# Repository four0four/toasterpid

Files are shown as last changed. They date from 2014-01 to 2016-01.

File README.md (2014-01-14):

# toasterpid

Firmware for my reflow oven PID controller (WIP!)

## Complete:
+ Simple serial driver
+ Thermocouple driver
+ LCD driver (4-bit, 8-bit)

## Work in progress:
+ PID algorithm/tuning
  + PID values don't differ much from 0 or 255, and given the oven's thermal momentum, they shouldn't...
+ Testing: Insulation in the oven

## Entirely untouched:
+ User interface

## Potential features:
+ USB instead of serial (final version will use an atmega16u4 or similar)
+ Serial (or USB) control

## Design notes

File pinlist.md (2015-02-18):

## AVR atmega168 pin listing

### Port B
+ Bit 0 - NC
+ Bit 1 - NC 
+ Bit 2 - uSD CS
+ Bit 3 - SPI MOSI
+ Bit 4 - SPI MISO
+ Bit 5 - SPI CLK
+ Bit 6 - AVR clk input (from enc28j60)
+ Bit 7 - SSR output (can we do this with clkin on b6?)

### Port C
+ Bit 0 - NC
+ Bit 1 - LCD EN
+ Bit 2 - LCD RS
+ Bit 3 - LCD R/W
+ Bit 4 - PHY reset
+ Bit 5 - PHY interrupt
+ Bit 6 - AVR reset
+ Bit 7 - Not pinned out

### Port D
+ Bit 0 - LCD bus bit 4 (0 in 4bit)
+ Bit 1 - LCD bus bit 5 (1 in 4bit)
+ Bit 2 - LCD bus bit 6 (2 in 4bit)
+ Bit 3 - LCD bus bit 7 (3 in 4bit)
+ Bit 4 - PHY CS
+ Bit 5 - Daughter CS (Thermo amp CS)
+ Bit 6 - Daughter LED 1
+ Bit 7 - Daughter LED 2

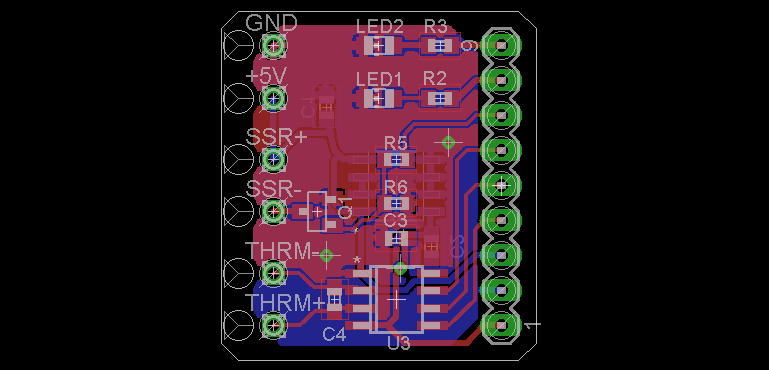
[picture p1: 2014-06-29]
hardware/images/daughter-brd.png

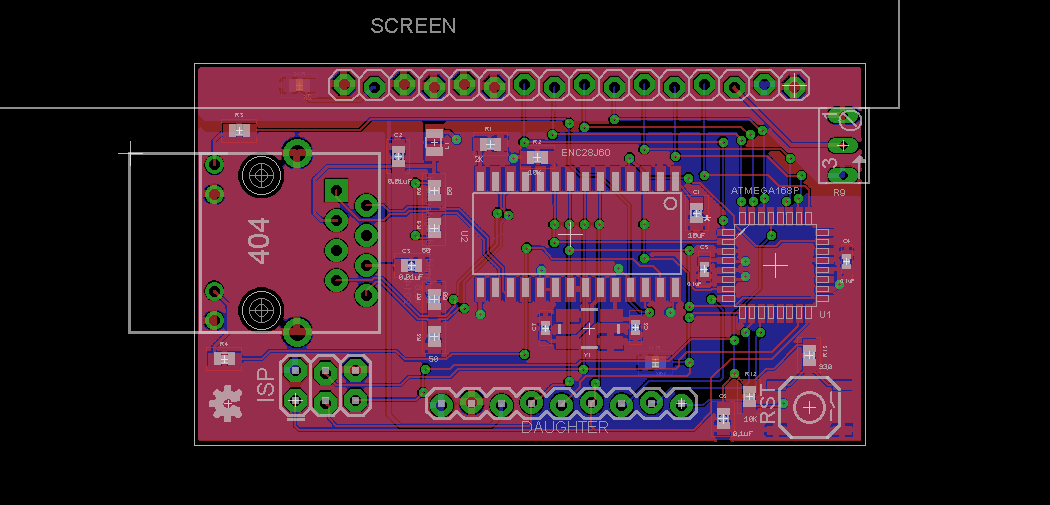
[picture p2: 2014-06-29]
hardware/images/main-brd.png

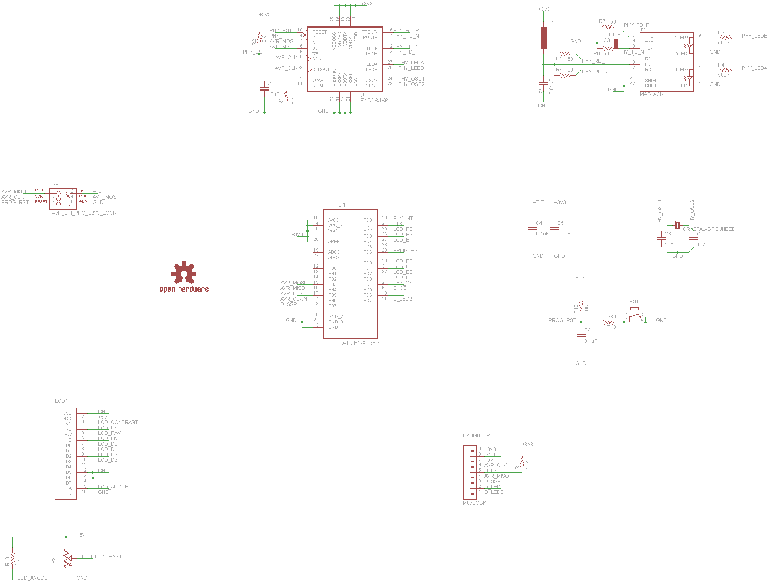
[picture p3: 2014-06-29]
hardware/images/main-sch.png

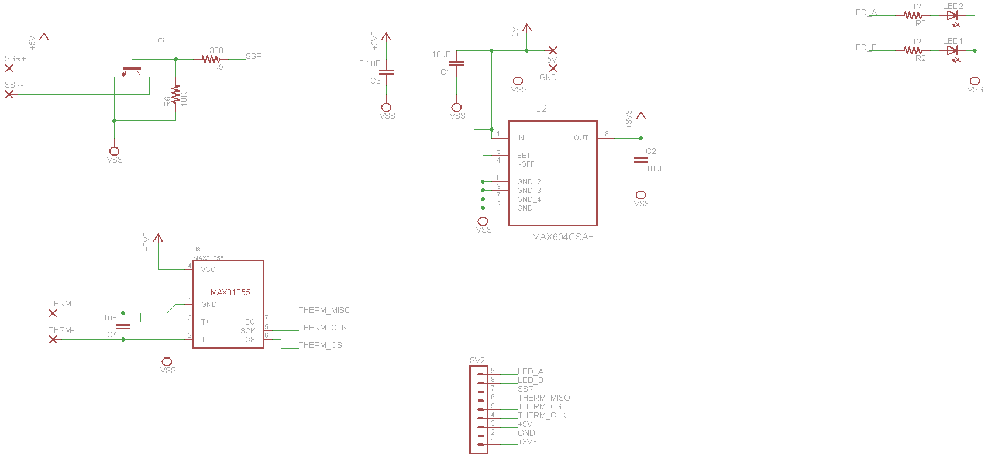
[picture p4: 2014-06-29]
hardware/images/daughter-sch.png

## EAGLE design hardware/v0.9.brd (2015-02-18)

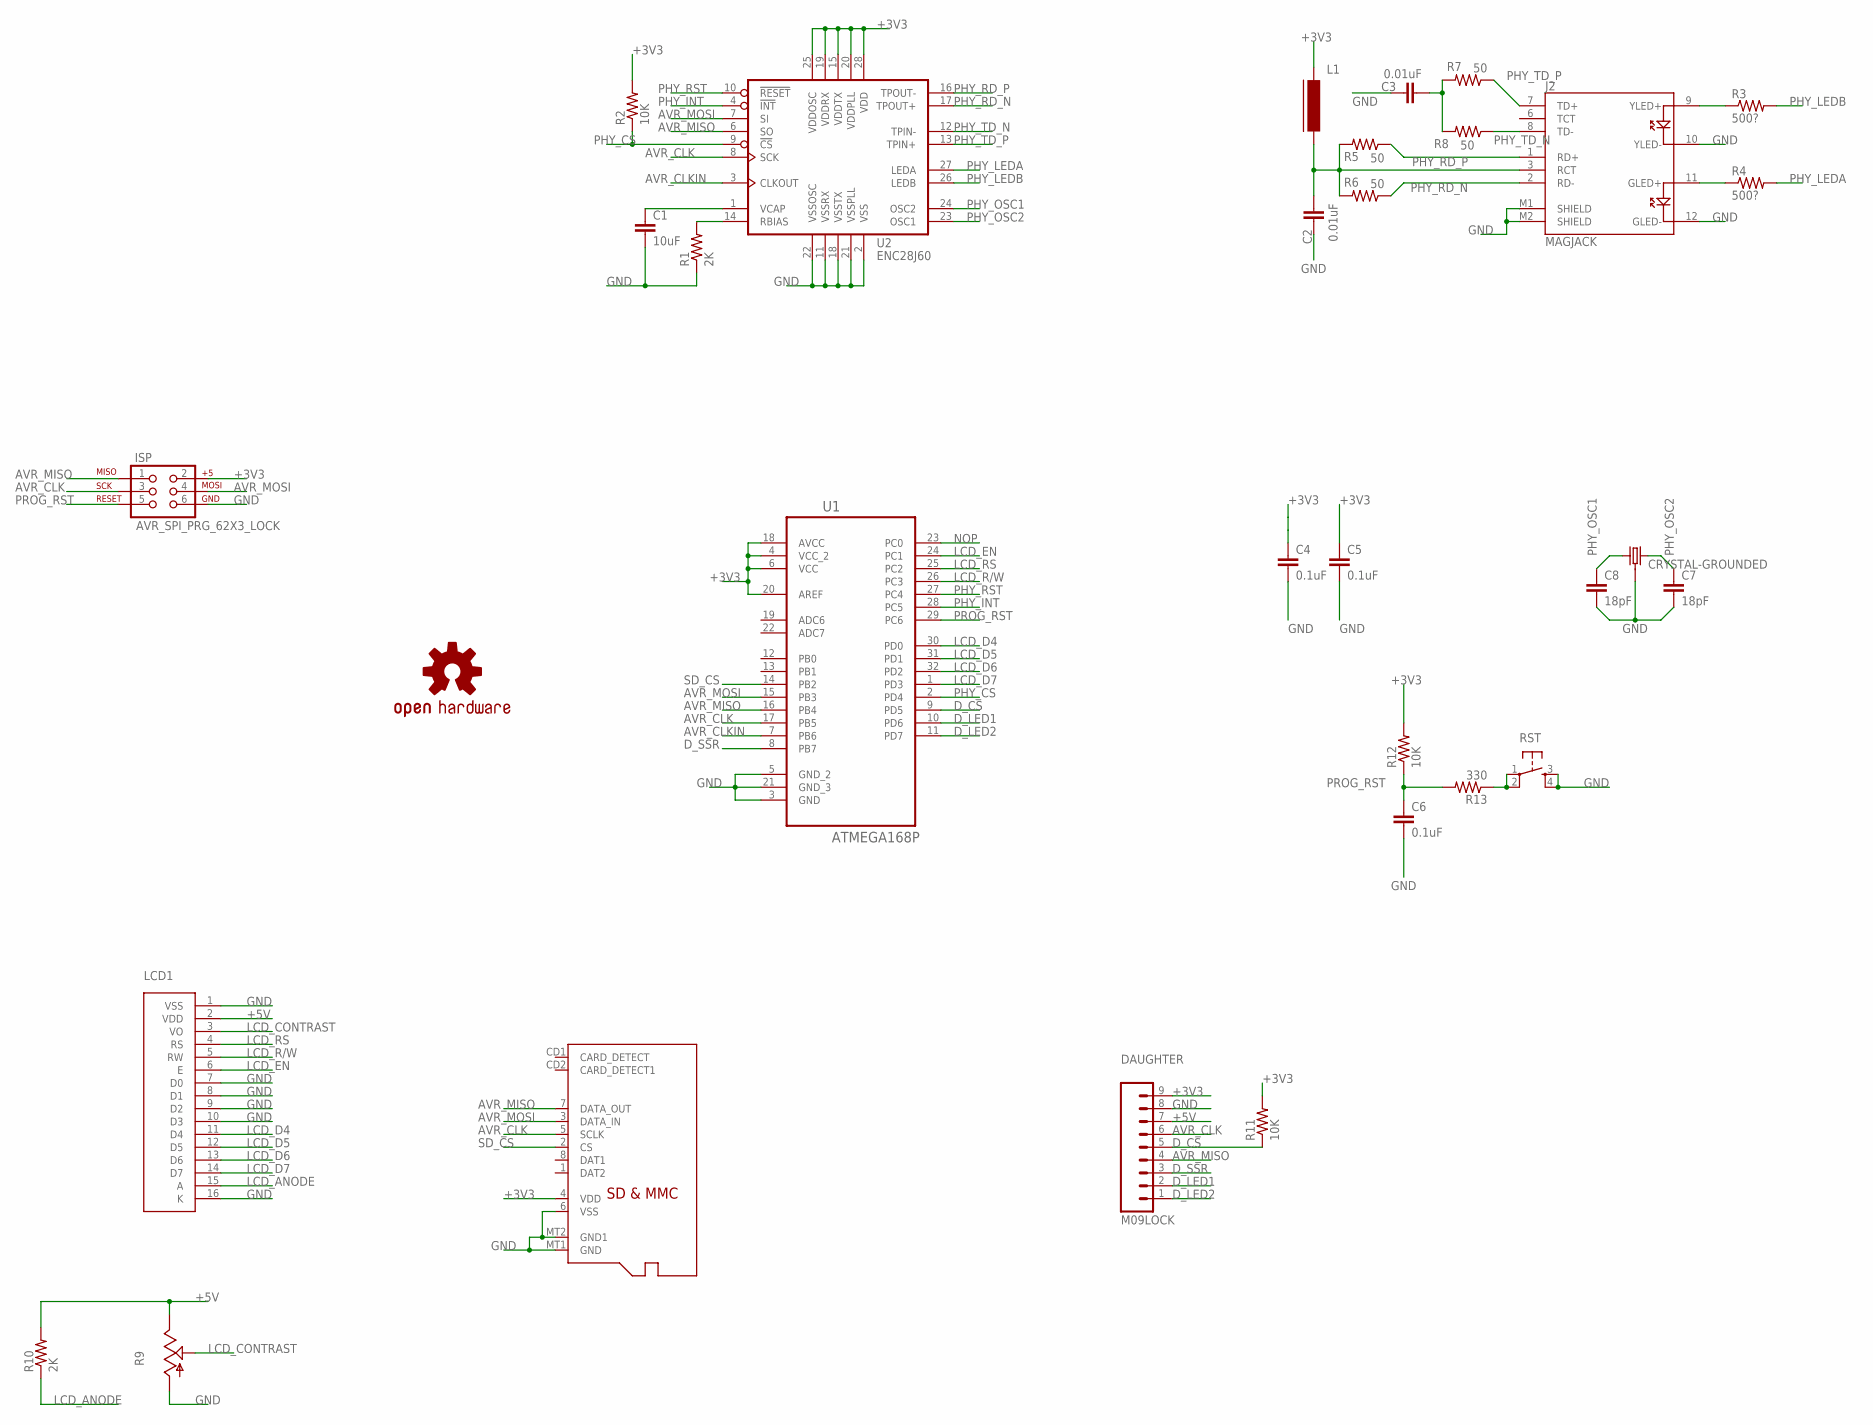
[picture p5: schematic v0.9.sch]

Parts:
C1: 10uF; 0603-CAP
C2, C3: 0.01uF; 0603-CAP
C4, C5: 0.1uF; 0402-CAP
C6: 0.1uF; 0603-CAP
C7, C8: 18pF; 0402-CAP
DAUGHTER: M09LOCK; 1X09_LOCK
ISP: AVR_SPI_PRG_62X3_LOCK; 2X3_LOCK
J2: MAGJACK
L1: FERRITE-0603; FB603
LCD1: HD44780; .1"16PIN
LOGO1: OSHW-LOGOS; OSHW-LOGO-S
R1, R10: 2K; 0603-RES
R2, R11, R12: 10K; 0603-RES
R3, R4: 500?; 0603-RES
R5, R6, R7, R8: 50; 0603-RES
R9: TRIM_US-B64Y; B64Y
R13: 330; 0603-RES
RST: TAC_SWITCHSMD; TACTILE-SWITCH-SMD
SD: MICROSD
U1: ATMEGA168P; QFP80P900X900X120-32N
U2: ENC28J60; SOIC-28W
Y1: CRYSTAL-GROUNDED; CRYSTAL-SMD-5X3

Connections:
+3V3: C4.1, C5.1, DAUGHTER.9, ISP.2, L1.1, R2.2, R11.2, R12.2, SD.4 (VDD), U1.4 (VCC_2), U1.6 (VCC), U1.18 (AVCC), U1.20 (AREF), U2.15 (VDDTX), U2.19 (VDDRX), U2.20 (VDDPLL), U2.25 (VDDOSC), U2.28 (VDD)
+5V: DAUGHTER.7, LCD1.2 (VDD), R9.E, R10.2
AVR_CLK: DAUGHTER.6, ISP.3, SD.5 (SCLK), U1.17 (PB5), U2.8 (SCK)
AVR_CLKIN: U1.7 (PB6), U2.3 (CLKOUT)
AVR_MISO: DAUGHTER.4, ISP.1, SD.7 (DATA_OUT), U1.16 (PB4), U2.6 (SO)
AVR_MOSI: ISP.4, SD.3 (DATA_IN), U1.15 (PB3), U2.7 (SI)
D_CS: DAUGHTER.5, R11.1, U1.9 (PD5)
D_LED1: DAUGHTER.2, U1.10 (PD6)
D_LED2: DAUGHTER.1, U1.11 (PD7)
D_SSR: DAUGHTER.3, U1.8 (PB7)
GND: C1.2, C2.1, C3.1, C4.2, C5.2, C6.2, C7.2, C8.2, DAUGHTER.8, ISP.6, J2.10 (YLED-), J2.12 (GLED-), J2.M1 (SHIELD), J2.M2 (SHIELD), LCD1.1 (VSS), LCD1.7 (D0), LCD1.8 (D1), LCD1.9 (D2), LCD1.10 (D3), LCD1.16 (K), R1.1, R9.A, RST.3, RST.4, SD.6 (VSS), SD.MT1 (GND), SD.MT2 (GND1), U1.3 (GND), U1.5 (GND_2), U1.21 (GND_3), U2.2 (VSS), U2.11 (VSSRX), U2.18 (VSSTX), U2.21 (VSSPLL), U2.22 (VSSOSC), Y1.2 (3), Y1.4 (3)
LCD_ANODE: LCD1.15 (A), R10.1
LCD_CONTRAST: LCD1.3 (VO), R9.S
LCD_D4: LCD1.11 (D4), U1.30 (PD0)
LCD_D5: LCD1.12 (D5), U1.31 (PD1)
LCD_D6: LCD1.13 (D6), U1.32 (PD2)
LCD_D7: LCD1.14 (D7), U1.1 (PD3)
LCD_EN: LCD1.6 (E), U1.24 (PC1)
LCD_R/W: LCD1.5 (RW), U1.26 (PC3)
LCD_RS: LCD1.4 (RS), U1.25 (PC2)
unnamed: J2.11 (GLED+), R4.1
unnamed: J2.9 (YLED+), R3.1
unnamed: R13.1, RST.1, RST.2
unnamed: C1.1, U2.1 (VCAP)
unnamed: R1.2, U2.14 (RBIAS)
NOP: U1.23 (PC0)
PHY_CS: R2.1, U1.2 (PD4), U2.9 (!CS)
PHY_INT: U1.28 (PC5), U2.4 (!INT)
PHY_LEDA: R4.2, U2.27 (LEDA)
PHY_LEDB: R3.2, U2.26 (LEDB)
PHY_OSC1: C8.1, U2.24 (OSC2), Y1.3 (1)
PHY_OSC2: C7.1, U2.23 (OSC1), Y1.1 (2)
PHY_RD_N: J2.2 (RD-), R6.1, U2.17 (TPOUT+)
PHY_RD_P: J2.1 (RD+), R5.1, U2.16 (TPOUT-)
PHY_RST: U1.27 (PC4), U2.10 (!RESET)
PHY_TD_N: J2.8 (TD-), R8.1, U2.12 (TPIN-)
PHY_TD_P: J2.7 (TD+), R7.1, U2.13 (TPIN+)
PROG_RST: C6.1, ISP.5, R12.1, R13.2, U1.29 (PC6)
RCT: C2.2, J2.3 (RCT), L1.2, R5.2, R6.2
SD_CS: SD.2 (CS), U1.14 (PB2)
TDCAP: C3.2, R7.2, R8.2

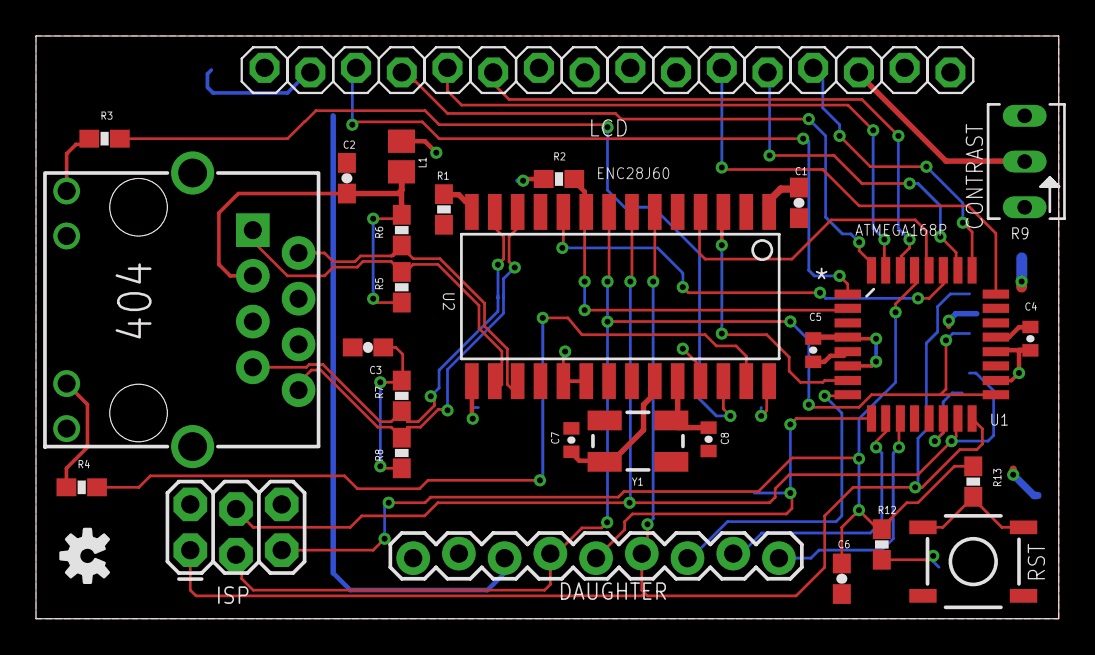
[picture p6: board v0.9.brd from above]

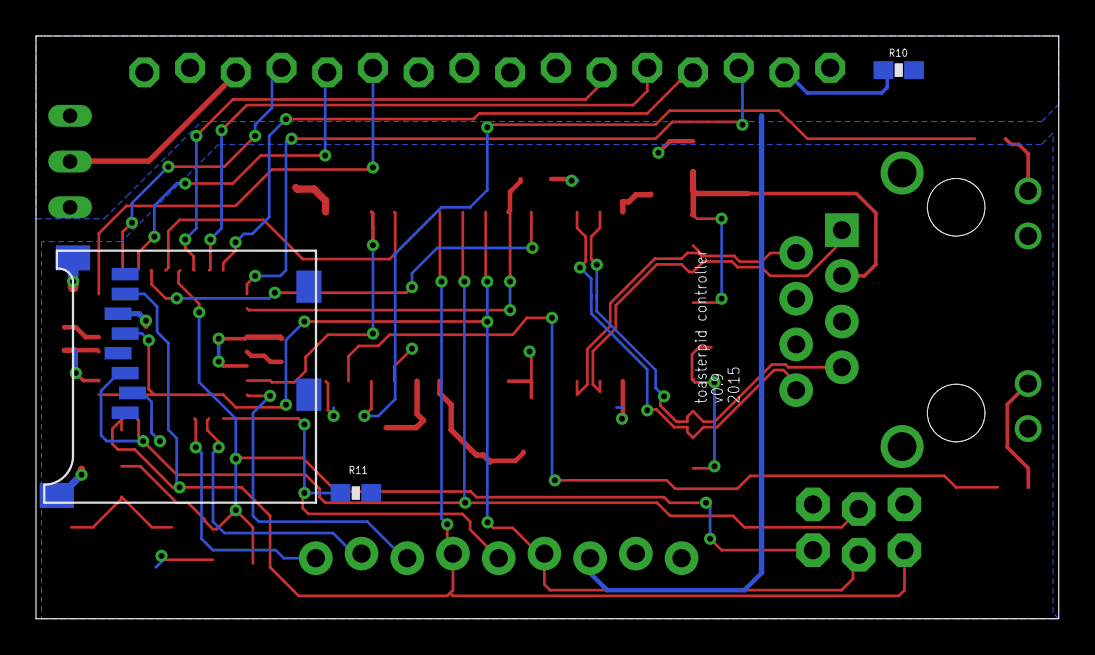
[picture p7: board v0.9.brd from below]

Board: 2 copper layers, 56.8 x 32.4 mm, 32 parts (3 on the bottom side), 40 nets.

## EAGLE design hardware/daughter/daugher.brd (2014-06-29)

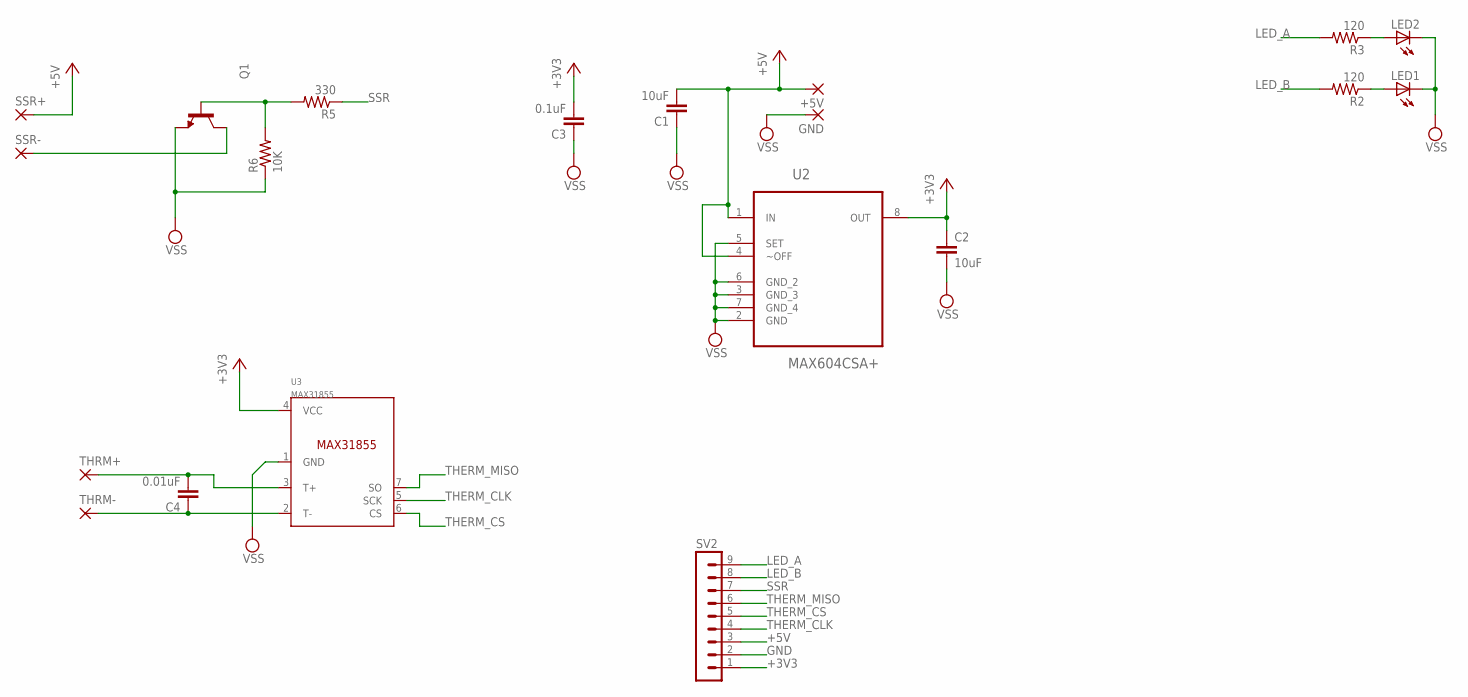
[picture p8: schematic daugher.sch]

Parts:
+5V: 1,6/0,8
C1, C2: 10uF; C0603
C3: 0.1uF; C0603
C4: 0.01uF; C0603
GND: 1,6/0,8
LED1, LED2: LEDCHIP-LED0805; CHIP-LED0805
Q1: BC849SMD; SOT23-BEC
R2, R3: 120; R0603
R5: 330; R0603
R6: 10K; R0603
SSR+: 1,6/0,8
SSR-: 1,6/0,8
SV2: MA09-1
THRM+: 1,6/0,8
THRM-: 1,6/0,8
U2: MAX604CSA+; SOIC127P600X175-8N
U3: MAX31855; SOIC8

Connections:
+3V3: C2.1, C3.2, SV2.1, U2.8 (OUT), U3.4 (VCC)
+5V: +5V.1, C1.2, SSR+.1, SV2.3, U2.1 (IN), U2.4 (~OFF)
GND: C1.1, C3.1, GND.1, LED1.C, LED2.C, Q1.E, R6.1, SV2.2, U2.2 (GND), U2.3 (GND_3), U2.5 (SET), U2.6 (GND_2), U2.7 (GND_4), U3.1 (GND)
GND1: Q1.C, SSR-.1
LED_A: R3.2, SV2.9
LED_B: R2.2, SV2.8
unnamed: C4.1, THRM-.1, U3.2 (T-)
unnamed: C4.2, THRM+.1, U3.3 (T+)
unnamed: LED1.A, R2.1
unnamed: LED2.A, R3.1
unnamed: Q1.B, R5.2, R6.2
SSR: R5.1, SV2.7
THERM_CLK: SV2.4, U3.5 (SCK)
THERM_CS: SV2.5, U3.6 (CS)
THERM_MISO: SV2.6, U3.7 (SO)
VSS: C2.2

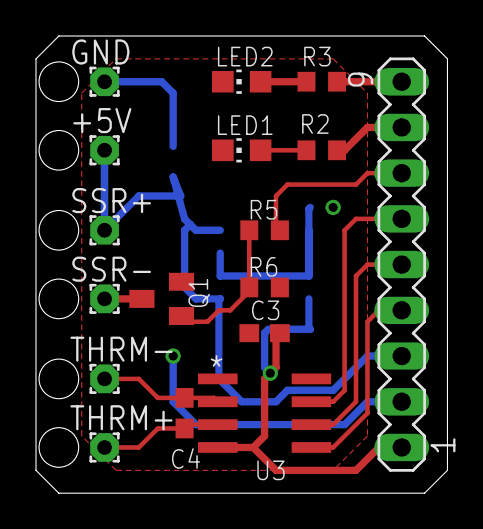
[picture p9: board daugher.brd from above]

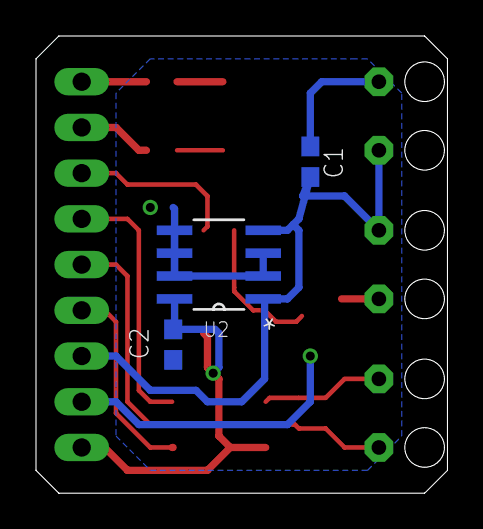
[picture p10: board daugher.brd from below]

Board: 2 copper layers, 22.9 x 25.4 mm, 20 parts (3 on the bottom side), 15 nets.

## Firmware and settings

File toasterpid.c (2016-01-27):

#include <avr/io.h>
#include <avr/interrupt.h>
#include <util/delay.h>
#include <stdio.h>

#include "serial.h"
#include "temp.h"
#include "lcd4bit.h"
//#include "sdcard.h"

// 10Hz flag for LCD/thermo/PID
#define _10HZ 0x80
// 2Hz flag for serial CSV data
#define _2HZ 0x40
// maximum number of steps per profile 
#define _MAX_STEPS 8
// cool-enough-to-handle (deg C)
#define _DONE_TEMP 30
// machine states
#define ERROR 0
#define IDLE 1
#define REFLOWING 2
#define COOLING 3
// PID gains
#define IGAIN 150
#define DGAIN 0
#define PGAIN 80
// integrator boundes
#define IMAX 200
#define IMIN -200
// name length per profile
// #define _NAME_LEN 8


// debug options
//#define _REALTIME
//#define _CSV

// set up timer interrupt hw
void timer_init();
// load (currently the only) profile from EEPROM to RAM globals
uint8_t load_profile();
// save (currently the only) profile to EEPROM
void save_profile();
// Interpolate stored profile values
void update_target();
// return 0-255 from PID algo
uint8_t get_pid(int16_t in);

// count to match ssr output to pid calculation
volatile uint8_t ssrCnt = 0;
// task flags 
volatile uint8_t flags = 0;
// 10hz counter
volatile uint8_t div10count = 0;
// 2hz counter
volatile uint8_t div50count = 0;
// 1hz counter
volatile uint8_t div100count = 0;
// current PID results
volatile uint8_t curPID = 0;
// current time (used to compute desired temp)
volatile uint16_t curTime = 0;


// TODO move most of these into proper scopes
// last error term 
int8_t lastError = 0;
// last integral term
int16_t lastIntegral = 0;
// current reflow oven state
uint8_t curState = IDLE;
// current step, saves time in getTemp(), may be useful elsewhere
uint8_t curStep = 0;
// current temperature read in from thermo
int16_t curTemp = 25;
// current target temperature, stored in 1/512 deg. no signs.
uint32_t curTarget = 50 * 512; 

// struct for profile data
typedef struct {
  uint8_t numSteps; // can be < _MAX_STEPS for a given profile, rest are not stored in EEPROM
  uint16_t stepTime[_MAX_STEPS]; // total time to spend at a given step/rate
  int16_t stepRate[_MAX_STEPS]; // dTemp for a given step, 1/512 deg/sec (>>9)
  uint8_t ceil[_MAX_STEPS]; // TODO REMOVE ME
#ifdef _NAME_LEN
  uint8_t name[_NAME_LEN];
#endif
} profile;

profile curProfile;

int main() {
  // for debug info via sprintf
  char str[20];
  uint8_t res = 0;
  uint8_t block[512] = {0};
  // last thermo read
  uint32_t lastRead = 0;

  // cludgy startup delay for external hw
  _delay_ms(100);  
  // temp. heartbeat
  DDRD |= (1<<6);
  PORTD &= ~(1<<6);

  // disable the phy for now
  DDRD |= (1<<4);
  PORTD |= (1<<4);

  // init hardware
  //serialInit();
  initThermo();
  lcd_init();
  timer_init();

  //res = sd_init();

  //sprintf(str,"res: 0x%x\n", res);
  //lcd_write_byte_str(str);

  /*
  lcd_write_char('1');
  res = sd_read_block(block, 0);
  lcd_write_char('2');
  if (res){
    sprintf(str,"ERROR: 0x%x\n", res);
    lcd_write_str(str);
  }
  else {
    for(int i = 40; i < 50; ++i){
      sprintf(str, "%x", block[i]);
      lcd_write_str(str);
    }
    lcd_write_str("\nDONE");
  }
  */

  //serialString("initialization completed.\n\r");
  //serialString("[time], [temp], [target], [pidval]\n\r");

  lcd_write_byte(RS_CMD, LCD_CLR);
  lastRead = readTemp();

  lcd_write_line(0, 2, "Thermocouple");

  load_profile();

  // good to go:
  sei();
  curState = REFLOWING;


  while(1) {
    if(flags & _10HZ){
      flags &= ~_10HZ;
      lastRead = readTemp();
      curTemp = getExternalTemp(lastRead);
      update_target();
      curPID = get_pid(curTemp);
      sprintf(str, "      %d%cC", curTemp,0xDF);
      if(getFaults(lastRead) == THERM_SCV_FAULT)
        lcd_write_line(1, 0, "Short to VCC (4)");
      else if(getFaults(lastRead) == THERM_SCG_FAULT)
        lcd_write_line(1, 0, "Short to GND (2)");
      else if(getFaults(lastRead) == THERM_OC_FAULT)
        lcd_write_line(1, 0, "Open probe (1)");
      else
        lcd_write_line(1, 0, str);
    }
    if(flags & _2HZ){
      flags &= ~_2HZ;
      if((curState == COOLING) && (curTemp <= _DONE_TEMP)){
        curState = IDLE;
        lcd_write_byte(RS_CMD, LCD_CLR); // clear display/buffer
        lcd_write_line(0, 6, "Done");
        cli();
      }
#ifdef _REALTIME
      // packet start token
      serialWrite(0xAB);
      serialWrite(0xCD);
      sprintf(str," %d %u \r",curTemp, curTime);
      serialString(str);
#endif
#ifdef _CSV
      sprintf(str,"%u, %d, %u, %u \n\r", curTime, curTemp, (uint16_t)(curTarget>>9), curPID);
      serialString(str);
#endif
    }
  }
}

void timer_init() {
  // No, this is not actually pwm. Handling a zero crossing SSR is possible in hardware, but ugly and (in my opinion) less effective.
  // 100 Hz interrupt

  TCCR1B |= (1<<WGM12); // enable CTC
  //OCR1A = 1875; // 100Hz at 12MHz, /64 
  OCR1A = 1250; // 100Hz at 8MHz, /64 
  TIMSK1 |= (1<<OCIE1A); // enable timer1 triggered interrupts
  TCCR1B |= (1<<CS11) | (1<<CS10); // div by 64
}

void update_target() {
  
  if(curTime > curProfile.stepTime[curStep]){
    ++curStep;
    if(curStep >= curProfile.numSteps){
      curState = COOLING;
      lcd_write_byte(RS_CMD, LCD_CLR); // clear display/buffer
      lcd_write_line(0, 4, "Cooling:");
      // This will just force the elements off, fine for now
      curTarget = 25 * 512;
      return;
    }
  }

  if((curState == REFLOWING) && ((curTarget>>9) < curProfile.ceil[curStep]))
    curTarget += curProfile.stepRate[curStep];
}

uint8_t load_profile() {
  // currently a single profile - Hardcoded crap
  // really could just use a single byte per temp step, max is *usually* < 255
  // TODO - Expand to multiple profiles
  // TODO - Allow for LCD+button profile selection/browsing
  // TODO get profile from EEPROM and stick it into global struct
  // Option: Store profile in target points + elapsed time format,
  //  then convert to internal format here.
  // ceilings added as a temporary ward against clock skew (interal RC osc)
  curProfile.numSteps = 4;
  curProfile.stepRate[0] = 1.3 * 512 / 10 ;
  curProfile.stepTime[0] = 90;
  curProfile.ceil[0] = 117;
  curProfile.stepRate[1] = 0.5 * 512 / 10;
  curProfile.stepTime[1] = 180;
  curProfile.ceil[1] = 162;
  curProfile.stepRate[2] = 1.5 * 512 / 10;
  curProfile.stepTime[2] = 210;
  curProfile.ceil[2] = 207;
  curProfile.stepRate[3] = -1.5 * 512 / 10;
  curProfile.stepTime[3] = 240;
  curProfile.ceil[3] = 255; // clumsy hack for a clumsy hack.
  
  return 0;
}

void save_profile() {
  // TODO write profile struct into EEPROM
  // TODO add serial interface for profile creation
}

uint8_t get_pid(int16_t in) {
  int16_t error = ((curTarget>>9) - curTemp);
  int32_t pterm = PGAIN * error;
  int32_t iterm = 0;
  int32_t dterm = (error - lastError) * DGAIN;

  lastError = error;

  if(lastIntegral + error > IMAX) iterm = IGAIN * IMAX;
  if(lastIntegral + error < IMIN) iterm = IGAIN * IMIN;
  else iterm = IGAIN * (lastIntegral + error);
  
  iterm += pterm + dterm;


  if(iterm >= 255)
    return 255;
  if(iterm <= 0)
    return 0;
  else
    return iterm;
}

ISR(TIMER1_COMPA_vect) {
  // update SSR state
  ++ssrCnt;
  if((ssrCnt <= curPID) && curState == REFLOWING)
    PORTD |= (1<<6);
  else
    PORTD &= ~(1<<6);

  if(div10count == 9){
    div10count = 0;
    flags |= _10HZ;
  }
  else
    ++div10count;
  if(div50count == 49){
    div50count = 0;
    flags |= _2HZ;
  }
  else
    ++div50count;
  if(div100count == 99){
    div100count = 0;
    ++curTime;
  }
  else
    ++div100count;
}

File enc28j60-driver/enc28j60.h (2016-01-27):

#include <stdint.h>
// SPI functions:
#include "serial.h"

// internal register definitions:

// Universal:
#define EIE 0x1B
#define EIR 0x1C
#define ESTAT 0x1D
#define ECON2 0x1E
#define ECON1 0x1F

// bits 7-5 aren't used, so...
#define _BANK0 0x20
#define _BANK1 0x40
#define _BANK2 0x80
#define _BANK3 0xA0
#define BANKMASK 0x1F

// Bank 0:
#define ERDPTL (0x00 | _BANK0)
#define ERDPTH (0x01 | _BANK0)
#define EWRPTL (0x02 | _BANK0)
#define EWRPTH (0x03 | _BANK0)
#define ETXSTL (0x04 | _BANK0)
#define ETXSTH (0x05 | _BANK0)
#define ETXNDL (0x06 | _BANK0)
#define ETXNDH (0x07 | _BANK0)
#define ERXSTL (0x08 | _BANK0)
#define ERXSTH (0x09 | _BANK0)
#define ERXNDL (0x0A | _BANK0)
#define ERXNDH (0x0B | _BANK0)
#define ERXRDPTL (0x0C | _BANK0)
#define ERXRDPTH (0x0D | _BANK0)
#define ERXWRPTL (0x0E | _BANK0)
#define ERXWRPTH (0x0F | _BANK0)
#define EDMASTL (0x10 | _BANK0)
#define EDMASTH (0x11 | _BANK0)
#define EDMANDL (0x12 | _BANK0)
#define EDMANDH (0x13 | _BANK0)
#define EDMADSTL (0x14 | _BANK0)
#define EDMADSTH (0x15 | _BANK0)
#define EDMACSL (0x16 | _BANK0)
#define EDMACSH (0x17 | _BANK0)

// Bank 1:
#define EHT0 (0x00 | _BANK1)
#define EHT1 (0x01 | _BANK1)
#define EHT2 (0x02 | _BANK1)
#define EHT3 (0x03 | _BANK1)
#define EHT4 (0x04 | _BANK1)
#define EHT5 (0x05 | _BANK1)
#define EHT6 (0x06 | _BANK1)
#define EHT7 (0x07 | _BANK1)
#define EPMM0 (0x08 | _BANK1)
#define EPMM1 (0x09 | _BANK1)
#define EPMM2 (0x0A | _BANK1)
#define EPMM3 (0x0B | _BANK1)
#define EPMM4 (0x0C | _BANK1)
#define EPMM5 (0x0D | _BANK1)
#define EPMM6 (0x0E | _BANK1)
#define EPMM7 (0x0F | _BANK1)
#define EPMCSL (0x10 | _BANK1)
#define EPMCSH (0x11 | _BANK1)
#define EPMOL (0x14 | _BANK1)
#define EPMOH (0x15 | _BANK1)
#define EWOLIE (0x16 | _BANK1)
#define EWOLIR (0x17 | _BANK1)
#define ERXFCON (0x18 | _BANK1)
#define EPKTCNT (0x19 | _BANK1)

// Bank 2:
#define MACON1 (0x00 | _BANK2)
#define MACON2 (0x01 | _BANK2)
#define MACON3 (0x02 | _BANK2)
#define MACON4 (0x03 | _BANK2)
#define MABBIPG (0x04 | _BANK2)
#define MAIPGL (0x06 | _BANK2)
#define MAIPGH (0x07 | _BANK2)
#define MACLCON1 (0x08 | _BANK2)
#define MACLCON2 (0x09 | _BANK2)
#define MAMXFLL (0x0A | _BANK2)
#define MAMXFLH (0x0B | _BANK2)
#define MAPHSUP (0x0D | _BANK2)
#define MICON (0x11 | _BANK2)
#define MICMD (0x12 | _BANK2)
#define MIREGADR (0x14 | _BANK2)
#define MIWRL (0x16 | _BANK2)
#define MIWRH (0x17 | _BANK2)
#define MIRDL (0x18 | _BANK2)
#define MIRDH (0x19 | _BANK2)

// Bank 3:
#define MAADR1 (0x00 | _BANK3)
#define MAADR0 (0x01 | _BANK3)
#define MAADR3 (0x02 | _BANK3)
#define MAADR2 (0x03 | _BANK3)
#define MAADR5 (0x04 | _BANK3)
#define MAADR4 (0x05 | _BANK3)
#define EBSTSD (0x06 | _BANK3)
#define EBSTCON (0x07 | _BANK3)
#define EBSTCSL (0x08 | _BANK3)
#define EBSTCSH (0x09 | _BANK3)
#define MISTAT (0x0A | _BANK3)
#define EREVID (0x12 | _BANK3)
#define ECOCON (0x15 | _BANK3)
#define EFLOCON (0x17 | _BANK3)
#define EPAUSL (0x18 | _BANK3)
#define EPAUSH (0x19 | _BANK3)

// PHY register definitions
#define PHCON1 0x00
#define PHSTAT1 0x01
#define PHID1 0x02
#define PHID2 0x03
#define PHCON2 0x10
#define PHSTAT2 0x11
#define PHIE 0x12
#define PHIR 0x13
#define PHLCON 0x14

// PHY SPI opcodes
#define RCR 0x0
#define RBM 0x1
#define WCR 0x2
#define WBM 0x3
#define BFS 0x4
#define BFC 0x5
#define SC  0x7


// general macros
#define enc_ctl_port  PORTD
#define enc_ctl_ddr   DDRD
#define enc_cs_pin    4
#define assert_enc_cs   enc_ctl_port &= ~(1<<enc_cs_pin) 
#define deassert_enc_cs enc_ctl_port |=  (1<<enc_cs_pin)


/*
  get/set enc registers - detect and set bank
  no bank set if: global control register /or/ PHY register
    there are no collisions.
*/
void set_enc_register(uint8_t reg, uint8_t d);
uint8_t get_enc_register(uint8_t reg);

/*
  get/set phy registers
void setEncPhyRegister(uint16_t reg, uint16_t d);
uint16_t getEncPhyRegister(uint16_t reg);
*/

// push len bytes from *data to the phy
void write_enc_mem(uint8_t *data, uint16_t len);

// array must be allocated and <= len
void read_enc_mem(uint8_t *data, uint16_t len);

//void setEncBit(

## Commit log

2013-08-30 preliminary thermocouple amp driver [untested]
2013-11-13 Added proper newline and overflow (into max of 32ch) support to LCD driver
2014-01-05 minor updates, started work on PID. added tick/interrupt
2014-01-06 PID added. TODO: clean up
2014-01-07 time source stability issues -> temporary ceiling value hack
    [toasterpid.c]
2014-01-07 overhauled target temp functionality. need to write PID function.
2014-01-07 fixed timer compare value
    [toasterpid.c]
2014-01-13 added 4 bit wide lcd driver
2014-01-13 fixed corner case with newlines
2014-06-29 added schematic/board eagle files
    [daugher.brd, daugher.sch, v0.6.brd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]
2014-07-11 Fixed tx diff pair impedence matching (hardware)
    [v0.6.brd, v0.6.sch]
2014-07-11 routed correct (upper) 4 bit lcd bus (hardware)
    [v0.6.brd, v0.6.sch]
2014-07-11 fixed last commit (hardware)
    [v0.6.brd]
2015-02-18 new hardware revision
    [v0.9.brd, v0.9.sch]
2015-02-18 added pin listing for the mcu
2015-05-22 fixed compilation errors in sd driver
    [sdcard.c, sdcard.h]
2015-05-25 current board revision config updates
2016-01-27 current sdcard code is utter trash, keeping this until rewritten. unfunctional.

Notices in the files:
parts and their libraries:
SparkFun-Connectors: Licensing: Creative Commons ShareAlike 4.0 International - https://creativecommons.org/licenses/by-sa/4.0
